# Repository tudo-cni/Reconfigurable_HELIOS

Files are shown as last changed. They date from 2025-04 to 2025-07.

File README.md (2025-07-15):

## Content of this Repository
This repository contains the code of the operation control center and SBC platform from our paper **Field Performance Evaluation of a
Mechatronic Reflector System in a Private mmWave Network Environment**.

If you use this code, please cite our original work in [Citation](#citation).

## Repository Structure
This paragraph describes the existing folder structure of the repository.
#### Main Folder
- **reconfigurable-helios-platform/**
  - Contains all project files and subfolders.  
##### Subfolders
- **Operation Control Center**
  - Contains all necessary files to run the operation control center
  - **angle mapping**
    - Contains the tables to convert the mechanical azimuth and elevation tilt angles alpha and beta to the corresponding servomotor angles from the top and bottom servomotor
  - **classes**
    - Contains the classes and methods for the operation control center
  - **configurations**
    - Configurations from the operation control center are saved in this folder in txt-files
  - **logos**
    - Contains the svg-files of TU Dortmund University and Communication Networks Institute logos for the operation control center
  - operation_control_center.py
    - Main file of the operation control center
- **Platform Code**
  - Contains the .py files, which run on the SBC

## Quick Start
#### Operation Control Center
This repository contains the code for the Operation Control Center, developed in Python.

To run the Operation Control Center, [NumPy](https://numpy.org/), [PySide6](https://pypi.org/project/PySide6/), to provide access to the QT6.0+ framework, and the [Qt-Material](https://qt-material.readthedocs.io/en/latest/index.html) packages are required.

The code has been tested with the following versions:
- Python: 3.13.0
- Numpy: 2.1.3
- PySide6: 6.9.0
- Qt-Material: 2.14

To start the operation control center, execute **"operation_control_center.py"**.

#### SBC Platform
To run the platform code, you must upload the necessary files from the "Platform Code" folder to the Raspberry Pi Pico, along with the two files "servo.py" and "pca9685.py" from the "[micropython-adafruit-pca9685](https://github.com/adafruit/micropython-adafruit-pca9685)" library.
Please note that these two files are not included in the folder and need to be downloaded from the specified library.

The "main.py" file will then be executed automatically upon starting the single-board computer (SBC).

## Acknowledgement
This work has been supported by the German Federal Ministry of Research, Technology and Space ([BMFTR](https://https://www.bundesregierung.de/breg-en/federal-government/ministries/federal-ministry-of-research-technology-and-space)) in the course of the
[6GEM Research Hub](https://www.6gem.de/en/) under the grant number 16KISK038.

## Citation
If you use this code in any of your publications, please cite our work (author's version) as:
```
@article{Haeger/etal/2025b,
	Author = {S. H{\"a}ger, M. Kaudewitz, F. Schmickmann, S. B{\"o}cker, and C. Wietfeld},
	Title = {Field Performance Evaluation of a Mechatronic Reflector System in a Private {mmWave} Network Environment},
	Journal = {IEEE Open Journal of the Communications Society},
	Month= jun, 
	Year = {2025},
	Vol = {6},
	Pages = {5005-5029},
	Doi = {10.1109/OJCOMS.2025.3572723},
	Project = {6GEM}, 
}
```

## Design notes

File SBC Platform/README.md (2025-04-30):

## SBC Platform
This folder contains the files that need to be uploaded to the SBC Platform, along with two additional files that are not included in this folder: "servo.py" and "pca9685.py" from the "[micropython-adafruit-pca9685](https://github.com/adafruit/micropython-adafruit-pca9685)" library.

Note: The values from the three calibrated positions of each servomotor obtained during the calibration process must be included in **calibration_function.py**!

- **main.py**
    - Is executed when the SBC platform is powered on.
- **wireless_module.py**
    - Initializes the wireless module of the SBC as an access point.
- **init_pca.py**
    - Initializes the two PCA9685 and the I2C connection between the PCAs and the SBC.
- **received_data_processing.py**
    - Method to convert received data string to numerical list.
- **calibration_function.py**
    - Method to calibrate the input values based on the calibration tables from the calibration procedure.
    - Note: The values from the calibration process are included here!
- **set_angle_functions.py**
    - Methods to set the PWM value of the corresponding PCA9685 outputs in order to achieve the desired mechanical tilt of the reflecting surface.

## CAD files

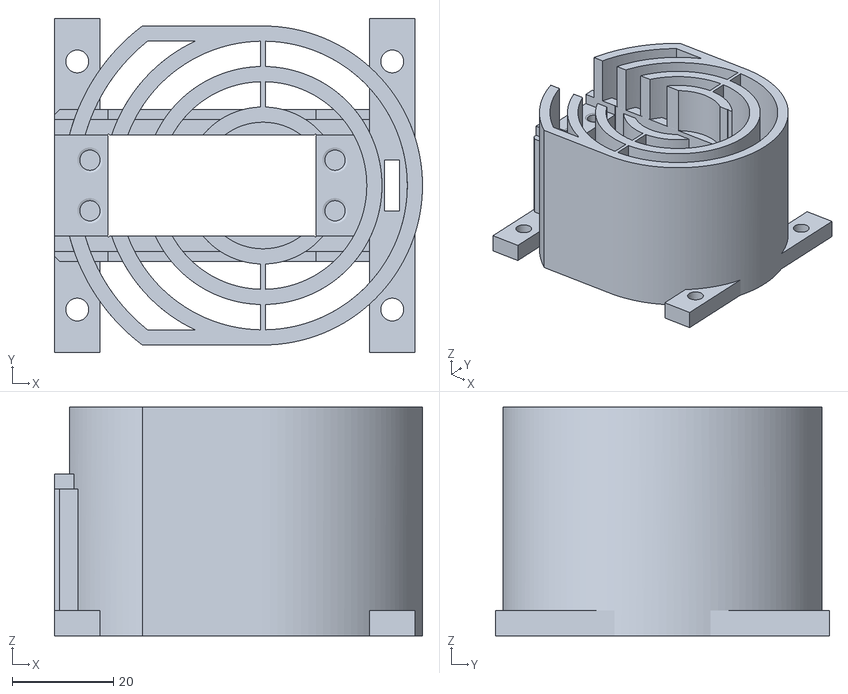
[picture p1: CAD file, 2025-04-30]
STL Module Files/Module_Base.stl
72.7 x 66.0 x 45.2

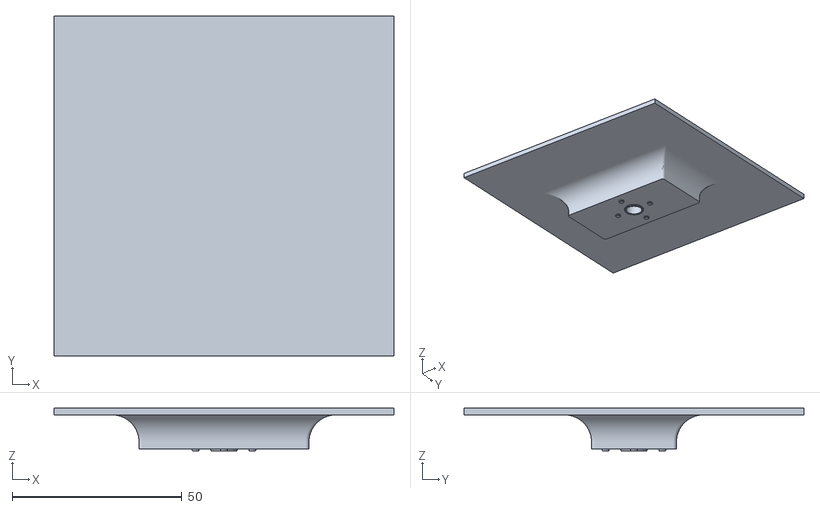
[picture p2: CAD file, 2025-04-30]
STL Module Files/Reflecting_Surface_Square10x10.stl
100.0 x 100.0 x 12.6

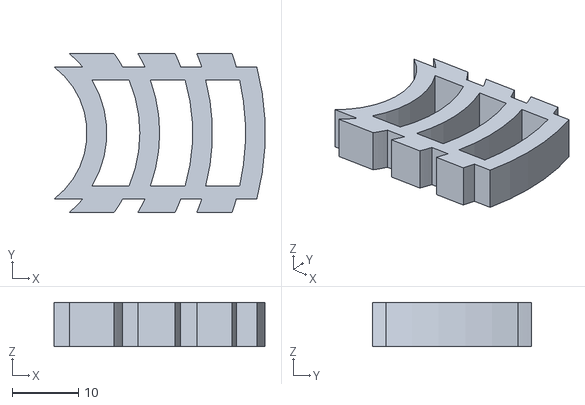
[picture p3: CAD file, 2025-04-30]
STL Module Files/Module_Plug.stl
31.9 x 24.0 x 6.70

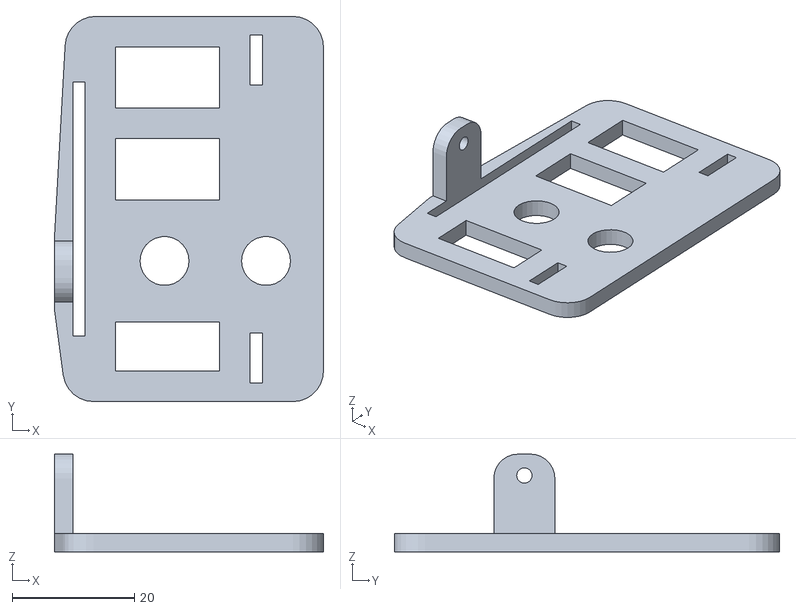
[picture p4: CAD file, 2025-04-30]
STL Module Files/Module_Plate.stl
44.0 x 63.0 x 16.0

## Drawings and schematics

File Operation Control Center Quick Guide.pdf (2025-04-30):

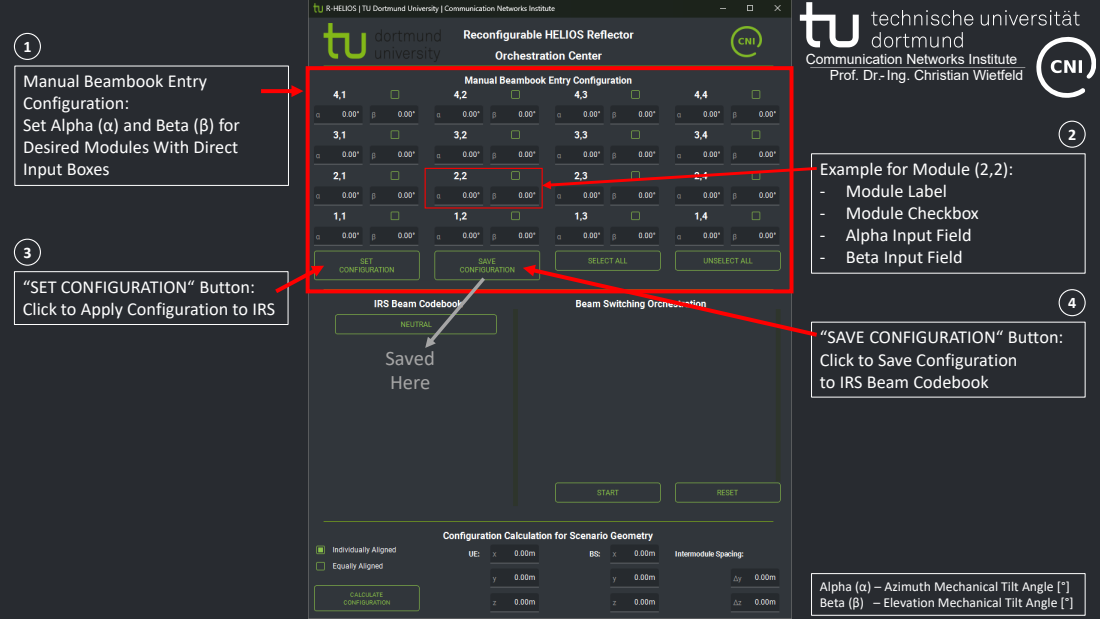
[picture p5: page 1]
Input Boxes; Example for Module (2,2):; Saved Here

Manual Beambook Entry
Configuration:
Set Alpha (α) and Beta (β) for
Desired Modules With Direct

- Module Label
- Module Checkbox
- Alpha Input Field
- Beta Input Field

“SET CONFIGURATION“ Button:
Click to Apply Configuration to IRS

“SAVE CONFIGURATION“ Button:
Click to Save Configuration
to IRS Beam Codebook

Alpha (α) – Azimuth Mechanical Tilt Angle [°]
Beta (β) – Elevation Mechanical Tilt Angle [°]

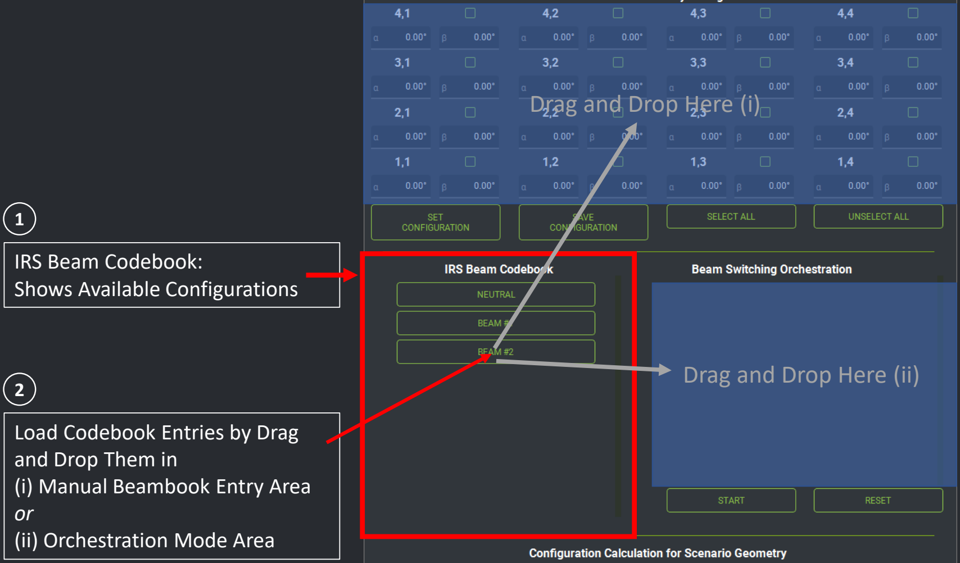
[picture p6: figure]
IRS Beam Codebook: Shows Available Configurations; Load Codebook Entries by Drag and Drop Them in (i) Manual Beambook Entry Area or (ii) Orchestration Mode Area; Drag and Drop Here (i); Drag and Drop Here (ii)

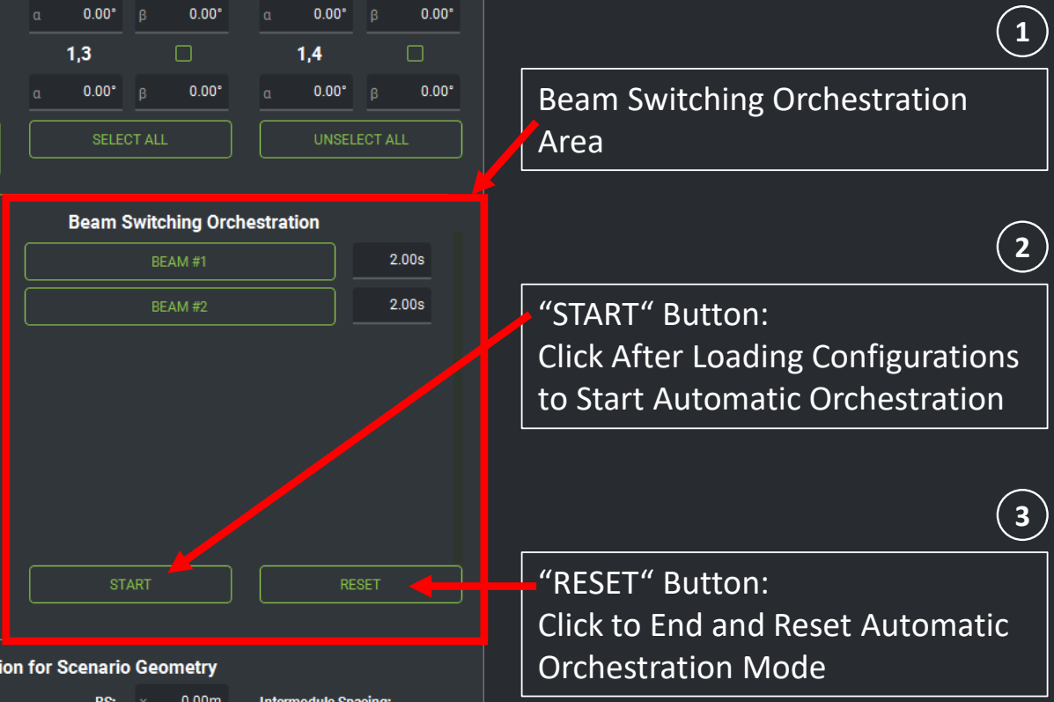
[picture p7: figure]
Beam Switching Orchestration Area; “START“ Button: Click After Loading Configurations to Start Automatic Orchestration; “RESET“ Button: Click to End and Reset Automatic Orchestration Mode
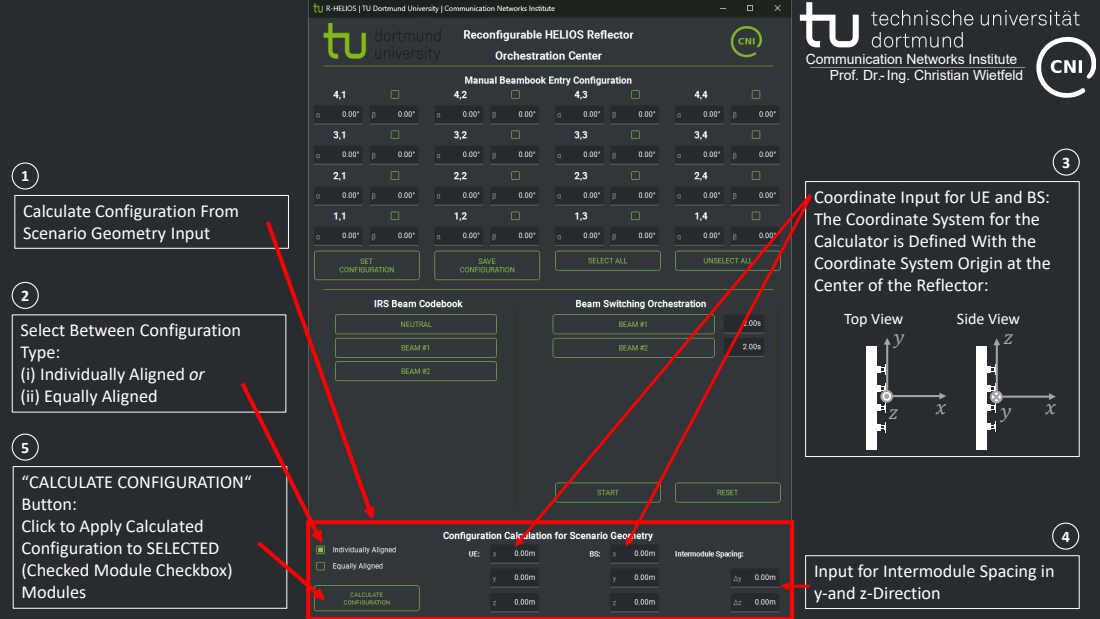
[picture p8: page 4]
Input for Intermodule Spacing in y-and z-Direction yz; Top View; Side View

Modules ¹²
Calculate Configuration From
Scenario Geometry Input

Coordinate Input for UE and BS:
The Coordinate System for the
Calculator is Defined With the
Coordinate System Origin at the
Center of the Reflector

Select Between Configuration
Type:
(i) Individually Aligned or
(ii) Equally Aligned

“CALCULATE CONFIGURATION“
Button:
Click to Apply Calculated
Configuration to SELECTED (Checked Module Checkbox)

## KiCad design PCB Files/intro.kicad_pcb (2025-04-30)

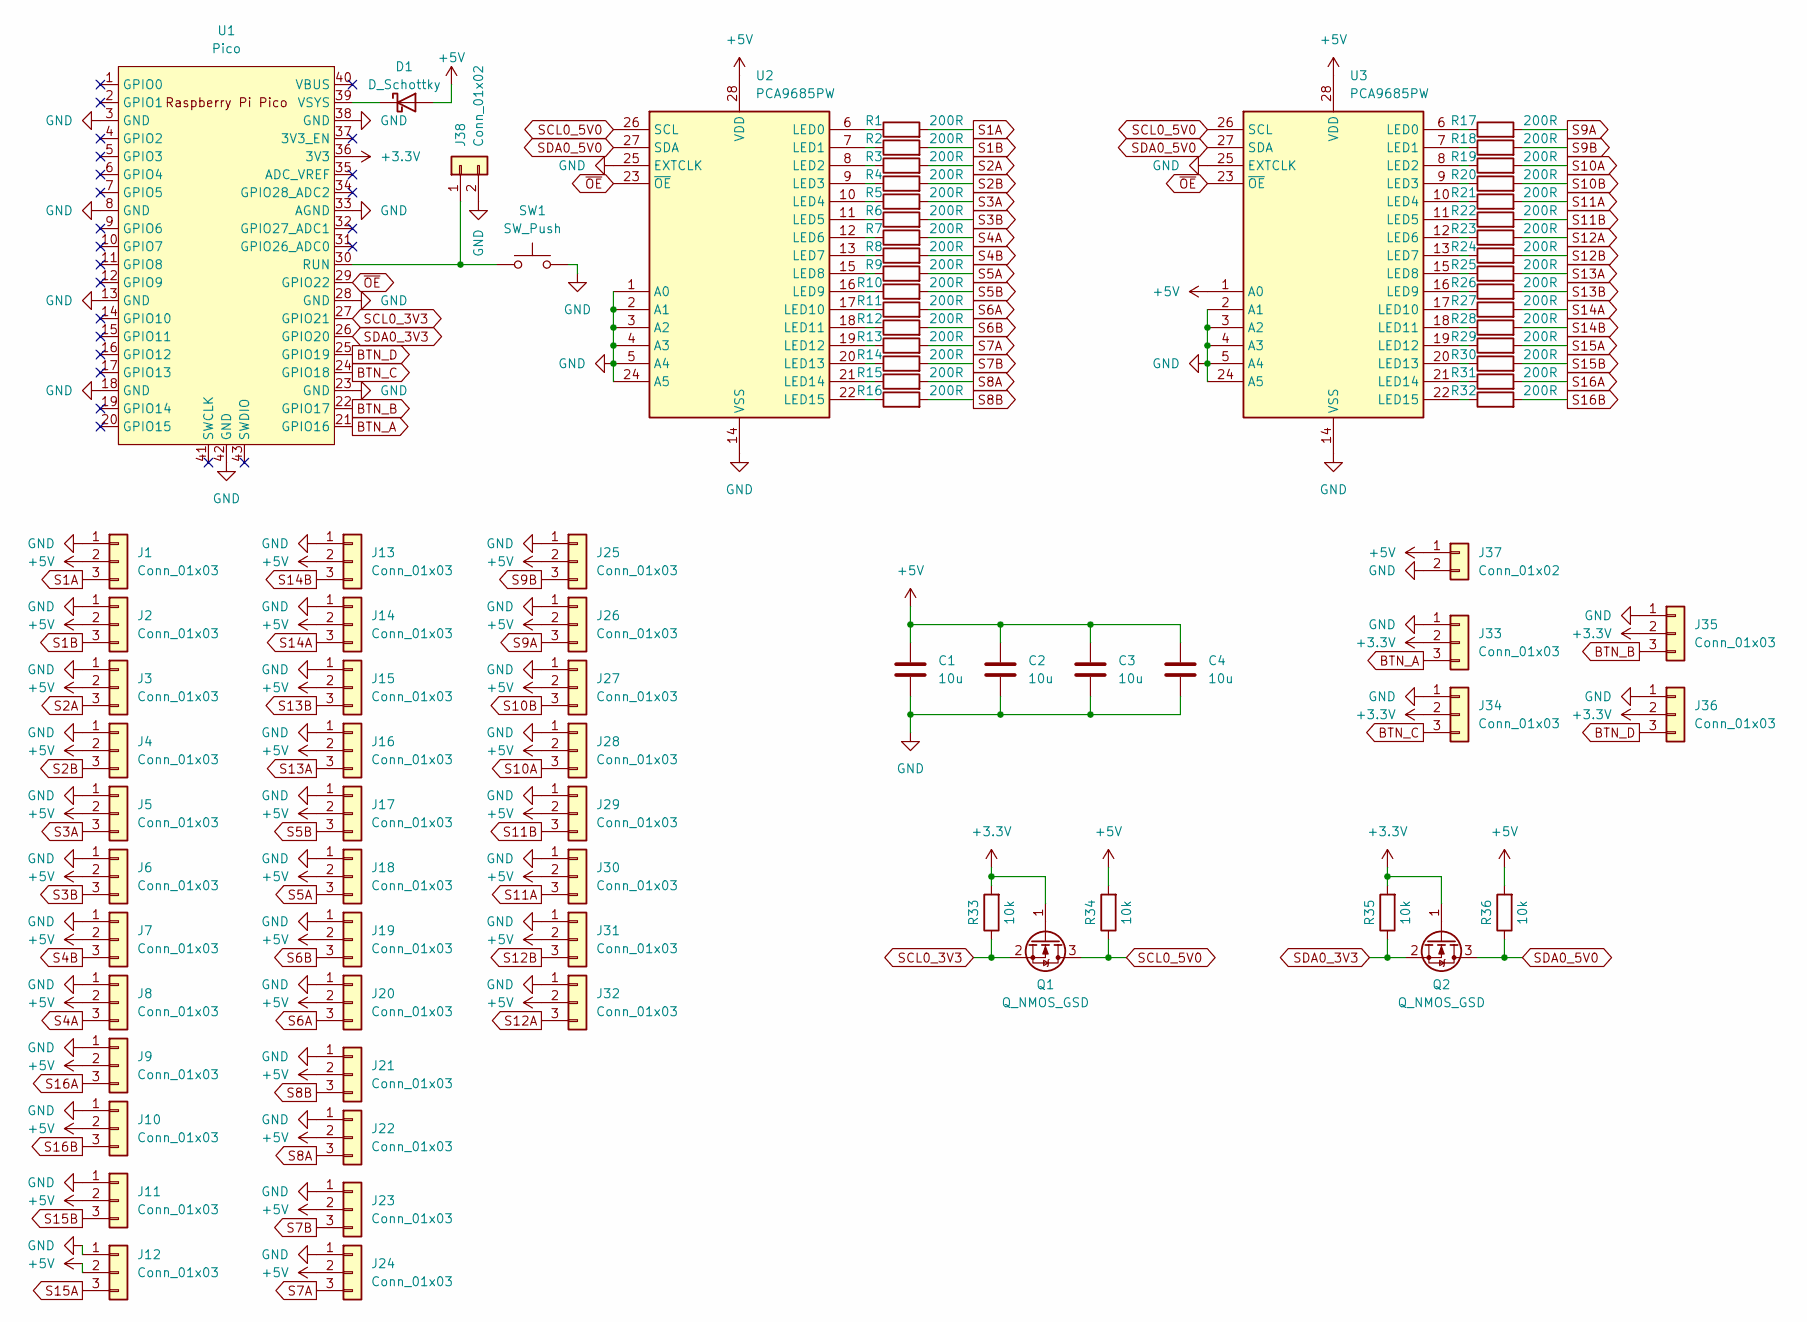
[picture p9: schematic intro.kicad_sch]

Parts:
C1, C2, C3, C4: 10u; C_0603_1608Metric
D1: D_Schottky; D_SOD-323_HandSoldering
J1, J2, J3, J4, J5, J6, J7, J8, J9, J10, J11, J12, J13, J14, J15, J16, J17, J18, J19, J20, J21, J22, J23, J24, J25, J26, J27, J28, J29, J30, J31, J32, J33, J34, J35, J36: Conn_01x03; PinHeader_1x03_P2.54mm_Vertical
J37: Conn_01x02; AMASS_XT60PW-M_1x02_P7.20mm_Horizontal
J38: Conn_01x02; PinHeader_1x02_P2.54mm_Vertical
Q1, Q2: Q_NMOS_GSD; SOT-23-3
R1, R2, R3, R4, R5, R6, R7, R8, R9, R10, R11, R12, R13, R14, R15, R16, R17, R18, R19, R20, R21, R22, R23, R24, R25, R26, R27, R28, R29, R30, R31, R32: 200R; R_0603_1608Metric
R33, R34, R35, R36: 10k; R_0603_1608Metric
SW1: SW_Push; SW_SPST_TL3342
U1: Pico; RPi_Pico_W_SMD_TH
U2, U3: PCA9685PW; TSSOP-28_4.4x9.7mm_P0.65mm

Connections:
+3.3V: J33.2, J34.2, J35.2, J36.2, Q1.1 (G), Q2.1 (G), R33.2, R35.2, U1.36 (3V3)
+5V: C1.1, C2.1, C3.1, C4.1, D1.2 (A), J1.2, J2.2, J3.2, J4.2, J5.2, J6.2, J7.2, J8.2, J9.2, J10.2, J11.2, J12.2, J13.2, J14.2, J15.2, J16.2, J17.2, J18.2, J19.2, J20.2, J21.2, J22.2, J23.2, J24.2, J25.2, J26.2, J27.2, J28.2, J29.2, J30.2, J31.2, J32.2, J37.1, R34.2, R36.2, U2.28 (VDD), U3.1 (A0), U3.28 (VDD)
BTN_A: J33.3, U1.21 (GPIO16)
BTN_B: J35.3, U1.22 (GPIO17)
BTN_C: J34.3, U1.24 (GPIO18)
BTN_D: J36.3, U1.25 (GPIO19)
GND: C1.2, C2.2, C3.2, C4.2, J1.1, J2.1, J3.1, J4.1, J5.1, J6.1, J7.1, J8.1, J9.1, J10.1, J11.1, J12.1, J13.1, J14.1, J15.1, J16.1, J17.1, J18.1, J19.1, J20.1, J21.1, J22.1, J23.1, J24.1, J25.1, J26.1, J27.1, J28.1, J29.1, J30.1, J31.1, J32.1, J33.1, J34.1, J35.1, J36.1, J37.2, J38.2, SW1.2, U1.3 (GND), U1.8 (GND), U1.13 (GND), U1.18 (GND), U1.23 (GND), U1.28 (GND), U1.33 (AGND), U1.38 (GND), U1.42 (GND), U2.1 (A0), U2.2 (A1), U2.3 (A2), U2.4 (A3), U2.5 (A4), U2.14 (VSS), U2.24 (A5), U2.25 (EXTCLK), U3.2 (A1), U3.3 (A2), U3.4 (A3), U3.5 (A4), U3.14 (VSS), U3.24 (A5), U3.25 (EXTCLK)
unnamed: D1.1 (K), U1.39 (VSYS)
unnamed: J38.1, SW1.1, U1.30 (RUN)
unnamed: R1.1, U2.6 (LED0)
unnamed: R2.1, U2.7 (LED1)
unnamed: R3.1, U2.8 (LED2)
unnamed: R4.1, U2.9 (LED3)
unnamed: R5.1, U2.10 (LED4)
unnamed: R6.1, U2.11 (LED5)
unnamed: R7.1, U2.12 (LED6)
unnamed: R8.1, U2.13 (LED7)
unnamed: R9.1, U2.15 (LED8)
unnamed: R10.1, U2.16 (LED9)
unnamed: R11.1, U2.17 (LED10)
unnamed: R12.1, U2.18 (LED11)
unnamed: R13.1, U2.19 (LED12)
unnamed: R14.1, U2.20 (LED13)
unnamed: R15.1, U2.21 (LED14)
unnamed: R16.1, U2.22 (LED15)
unnamed: R17.1, U3.6 (LED0)
unnamed: R18.1, U3.7 (LED1)
unnamed: R19.1, U3.8 (LED2)
unnamed: R20.1, U3.9 (LED3)
unnamed: R21.1, U3.10 (LED4)
unnamed: R22.1, U3.11 (LED5)
unnamed: R23.1, U3.12 (LED6)
unnamed: R24.1, U3.13 (LED7)
unnamed: R25.1, U3.15 (LED8)
unnamed: R26.1, U3.16 (LED9)
unnamed: R27.1, U3.17 (LED10)
unnamed: R28.1, U3.18 (LED11)
unnamed: R29.1, U3.19 (LED12)
unnamed: R30.1, U3.20 (LED13)
unnamed: R31.1, U3.21 (LED14)
unnamed: R32.1, U3.22 (LED15)
S1A: J1.3, R1.2
S1B: J2.3, R2.2
S2A: J3.3, R3.2
S2B: J4.3, R4.2
S3A: J5.3, R5.2
S3B: J6.3, R6.2
S4A: J8.3, R7.2
S4B: J7.3, R8.2
S5A: J18.3, R9.2
S5B: J17.3, R10.2
S6A: J20.3, R11.2
S6B: J19.3, R12.2
S7A: J24.3, R13.2
S7B: J23.3, R14.2
S8A: J22.3, R15.2
S8B: J21.3, R16.2
S9A: J26.3, R17.2
S9B: J25.3, R18.2
S10A: J28.3, R19.2
S10B: J27.3, R20.2
S11A: J30.3, R21.2
S11B: J29.3, R22.2
S12A: J32.3, R23.2
S12B: J31.3, R24.2
S13A: J16.3, R25.2
S13B: J15.3, R26.2
S14A: J14.3, R27.2
S14B: J13.3, R28.2
S15A: J12.3, R29.2
S15B: J11.3, R30.2
S16A: J9.3, R31.2
S16B: J10.3, R32.2
SCL0_3V3: Q1.2 (S), R33.1, U1.27 (GPIO21)
SCL0_5V0: Q1.3 (D), R34.1, U2.26 (SCL), U3.26 (SCL)
SDA0_3V3: Q2.2 (S), R35.1, U1.26 (GPIO20)
SDA0_5V0: Q2.3 (D), R36.1, U2.27 (SDA), U3.27 (SDA)
~OE: U1.29 (GPIO22), U2.23 (~OE), U3.23 (~OE)

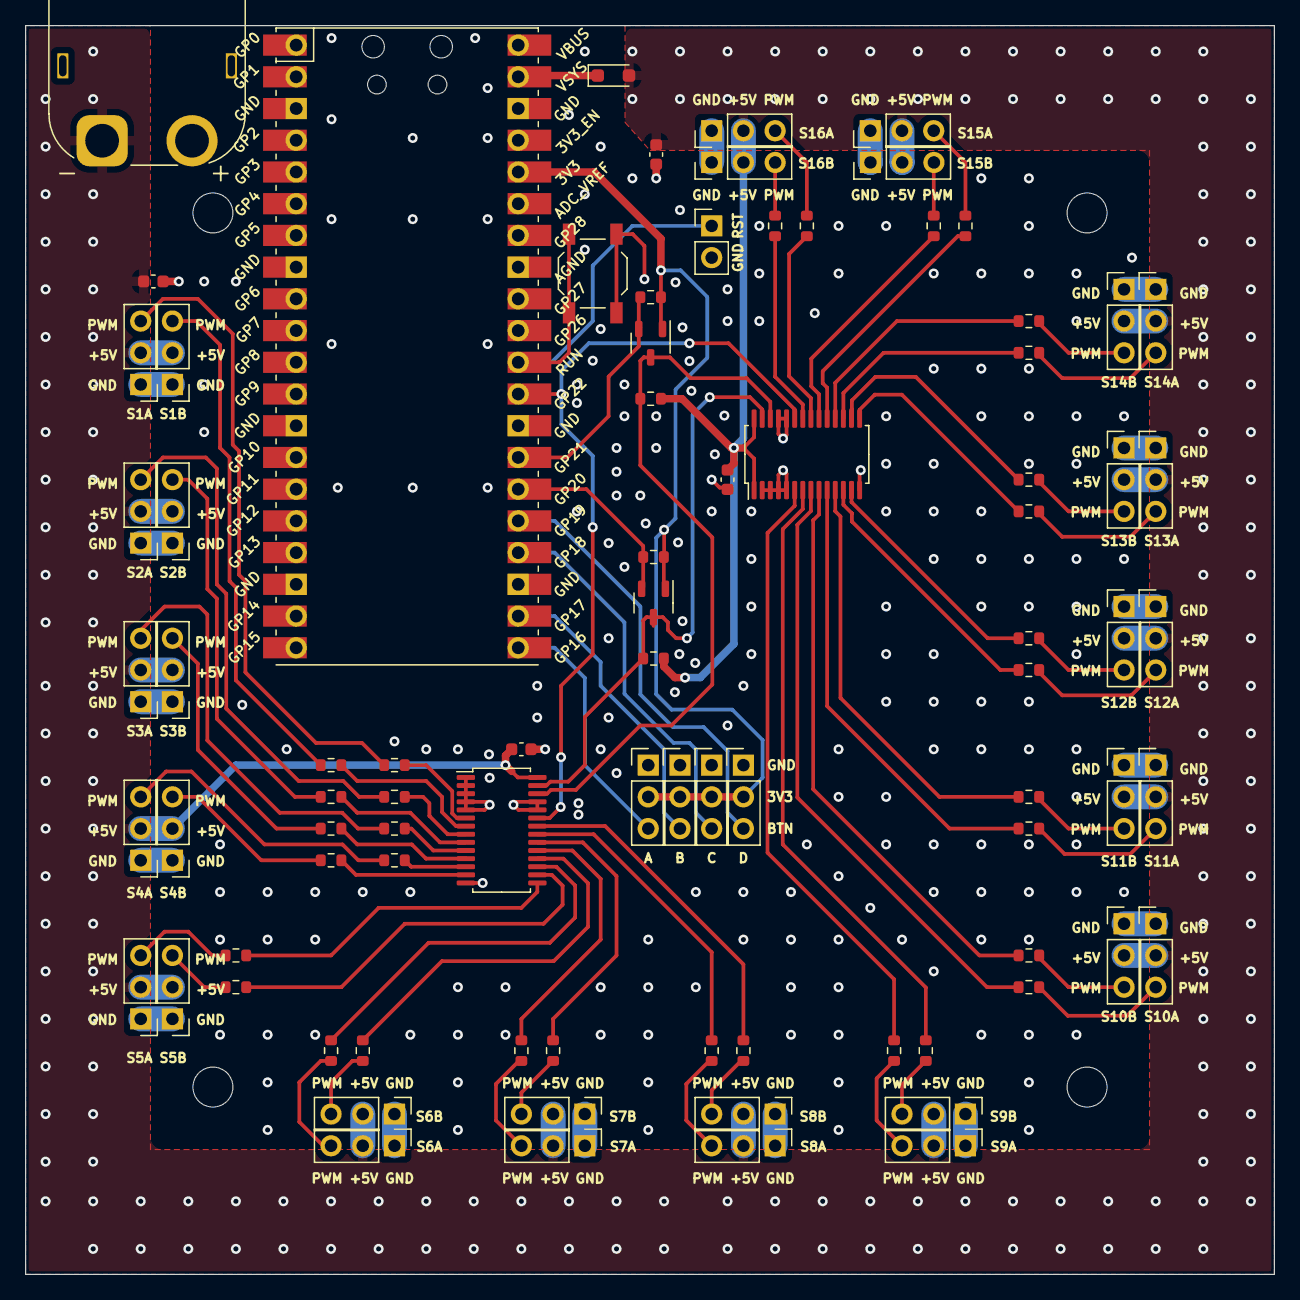
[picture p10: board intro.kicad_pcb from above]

Board: 4 copper layers, 100.0 x 100.0 mm, 85 parts (0 on the bottom side), 78 nets.

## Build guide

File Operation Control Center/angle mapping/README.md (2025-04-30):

## Angle Mapping Folder
This folder contains the angle mapping tables to convert azmuth tilt angle alpha and eleation tilt angle beta from the reflecting urface in the corresponding servomotor angles for the top and bottom servomotor.

Each file contains the table for the alpha angle of the file name and all beta angles from -60.00° up to 60.00° as a numpy file. 
For example the file "angle_map_alpha_5980.npy" contains for alpha=59.80° and all beta angles, with the first line of the file conatining the angles fop beta=-60.00° and the last line for beta=60.00° in 0.01° steps.

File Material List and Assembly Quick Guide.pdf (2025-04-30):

The Authors | Slide 1

Communication Networks Institute Prof. Dr.-Ing. Christian Wietfeld

Field Performance Evaluation of a Mechatronic Reflector System in a Private mmWave Network Environment

# Material List

| Quantity | Part | Assembly Step
1 | 11 | Aluminum Profile 20x20 Groove 6 B-Type, 1m | 1
2 | 16 | Internal 90° Angle/Bracket Groove 6 B-Type M5
3 | 32 | Screw M5x5
4 | 16 | Pan & Tilt Kit, cf. Paper
5 | 16 | Long “C“ Bracket (51mm(L) X 24mm(W) X 57mm(H))
6 | 16 | 3D-Printed Module (Base, Plug and Plate)
7 | 64 | M3x5.7 3D-Printing Threaded Insert
8 | 64 | Screw M3x7
9 | 16 | 3D-Printed Reflecting Surface
10 | 16 | Screw M5x8, with washer
11 | 16 | M5x9.5 3D-Printing Threaded Insert
12 | 1 | SBC (Raspberry Pi Pico W) | 3
13 | 2 | 16-Channel Pulse-Width Modulation Controller (PCA9685)
14 | 1 | Designed PCB
15 | 64 | Screw M3x7 | 4
16 | 64 | M3 Slot Nuts Groove 6
17 | 32 | Servomotor Extension Cable JR Male to Female, 1m | 5
18 | 1 | 5V Power Supply

2

# 1. Assembly Instruction – Frame

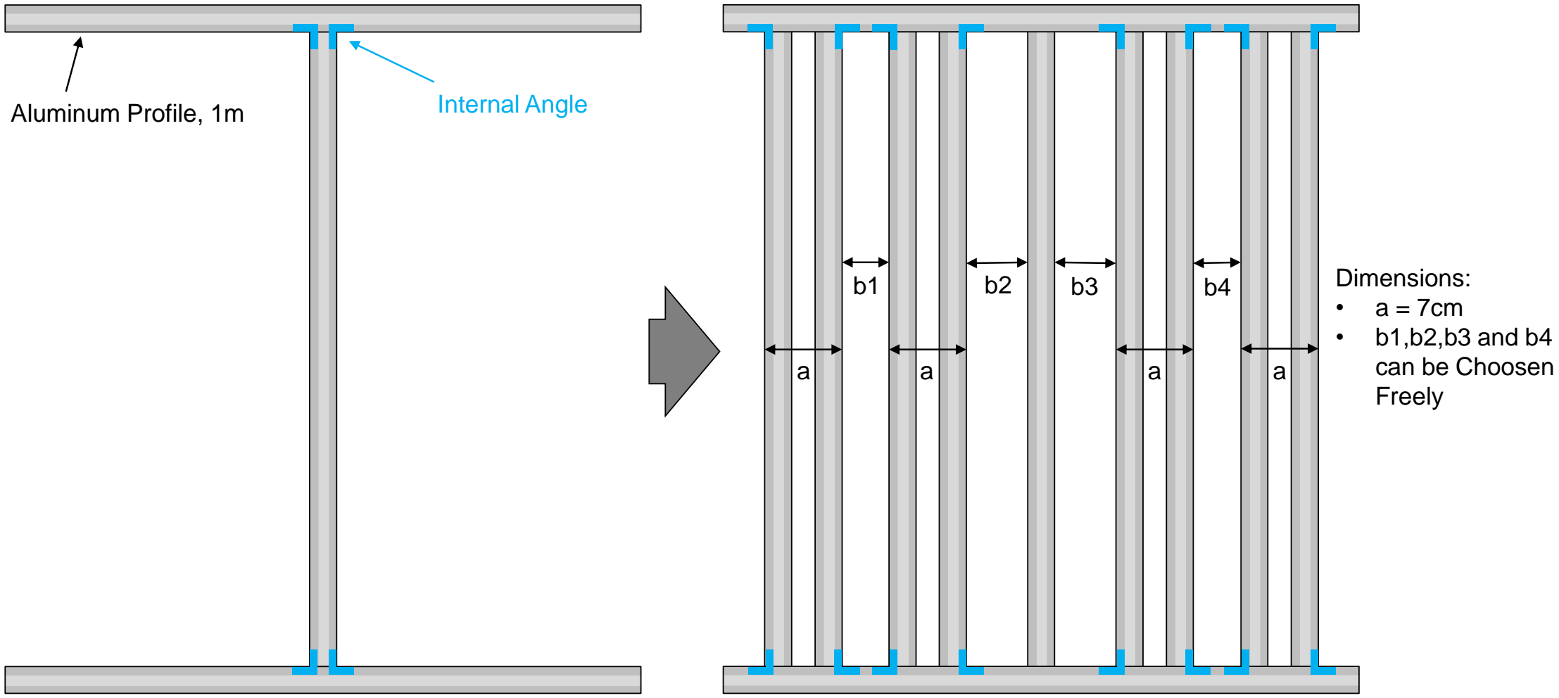
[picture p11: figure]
Aluminum Profile, 1m; Internal Angle; Dimensions:; • a = 7cm • b1,b2,b3 and b4 can be Choosen Freely

# 2. Assembly Instruction – Module (1)

1. Assemble 16 Modules, Each Consisting of Three 3D-Printed Components (Base, Plug, Plate) Along With the Pan & Tilt Kit)

## 2. Assemble in the Following Order:

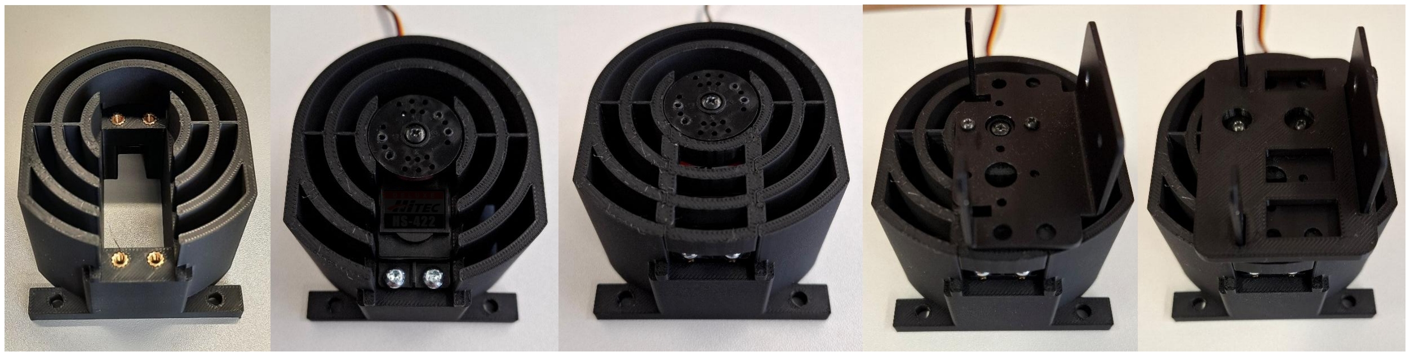
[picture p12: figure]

### 1. Start With the 3D-Printed Module Base with 4 M3x5.7 Threaded Inserts

### 2. Place First Servomotor in Module Base and Fixate it With 4 M3x7 Screws

### 3. Press the 3D-Printed Module Plug Into the Gap Until it Fits Cleanly With the Edges

### 4. Fixate the Multi-Purpose Servo Bracket From the Pan & Tilt Kit on the Servomotor

### 4. Place the 3D-Printed Module Plate on the Bracket

# 2. Assembly Instruction – Module (2)

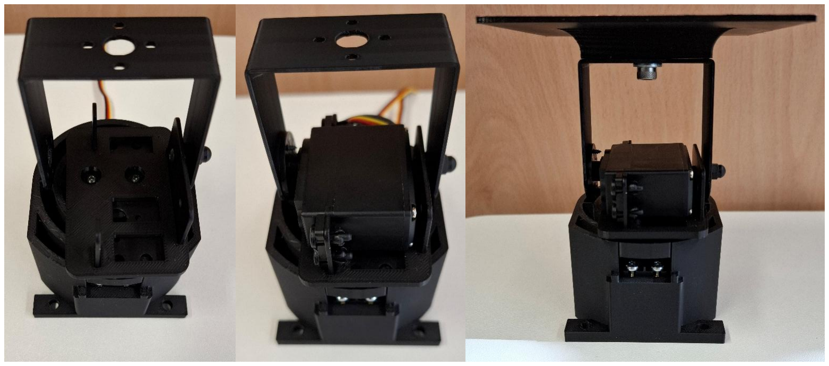
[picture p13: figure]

### 5. Mount Long “C“ Bracket Instead of Short “C“ Bracket From the Pan & Tilt Kit

### 6. Mount Second Servomotor as Specified by the Pan & Tilt Kit

### 7. Prepare the 3D-Printed Reflecting Surface With a M5x9.5 Threaded Insert. Mount the Reflecting Surface on the “C“ Bracket with

One M5x8 Screw With Washer.

3. On the 3D-Printed Reflecting Surface Self-Adhesive Copper Tape can be Applied or, for Example, a Conductive Coating can be

## Spray-Painted, to Achieve Desired Reflection Characteristics

# 3. Assembly Instruction – SBC and PCB Circuit Diagram

## 1. To Control the 32 Servomotor a SBC

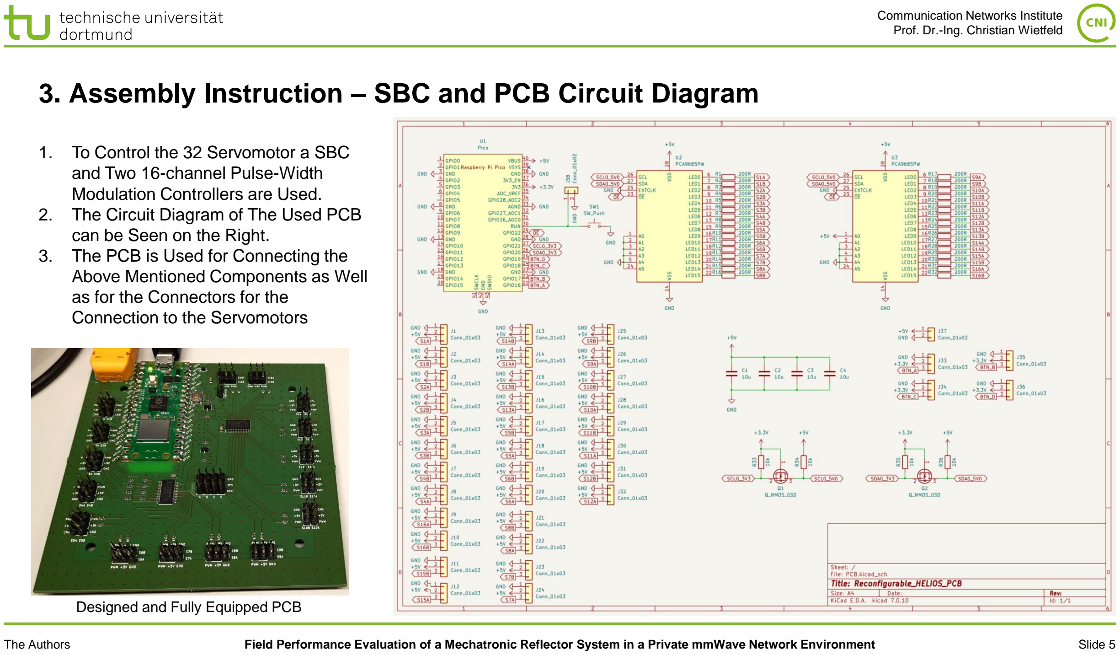
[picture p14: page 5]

## and Two 16-channel Pulse-Width

Modulation Controllers are Used.

## 2. The Circuit Diagram of The Used PCB

can be Seen on the Right.

## 3. The PCB is Used for Connecting the Above Mentioned Components as Well as for the Connectors for the Connection to the Servomotors

### Designed and Fully Equipped PCB

# 4. Assembly Instruction – Mount Modules on Frame

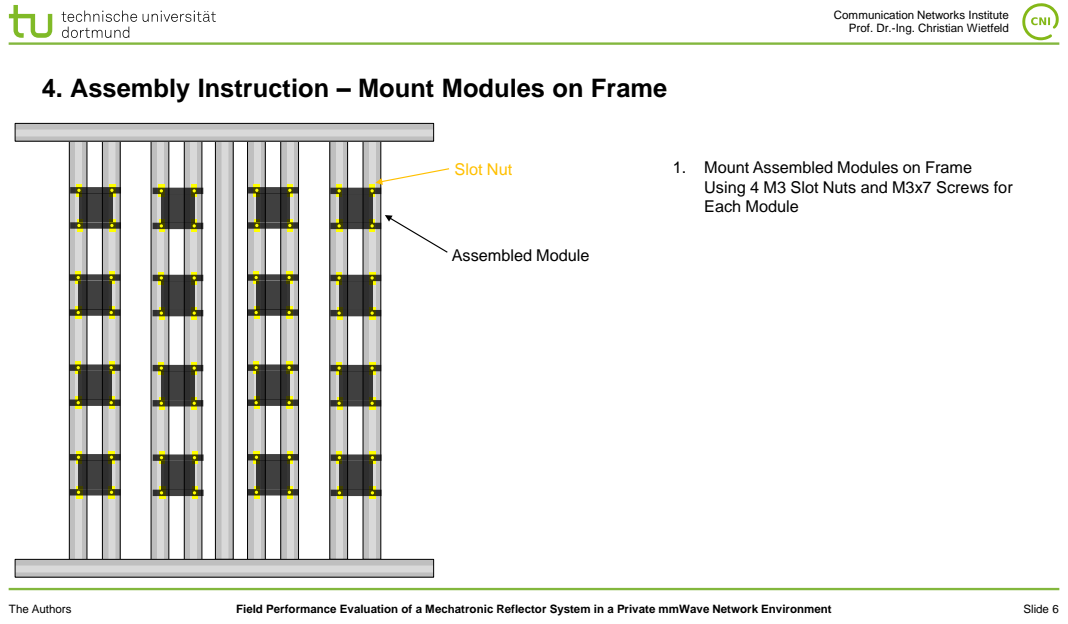
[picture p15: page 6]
Slot Nut; Assembled Module

1. Mount Assembled Modules on Frame
Using 4 M3 Slot Nuts and M3x7 Screws for
Each Module

# 5. Assembly Instruction – Connection Overview

## PCB Slot Overview

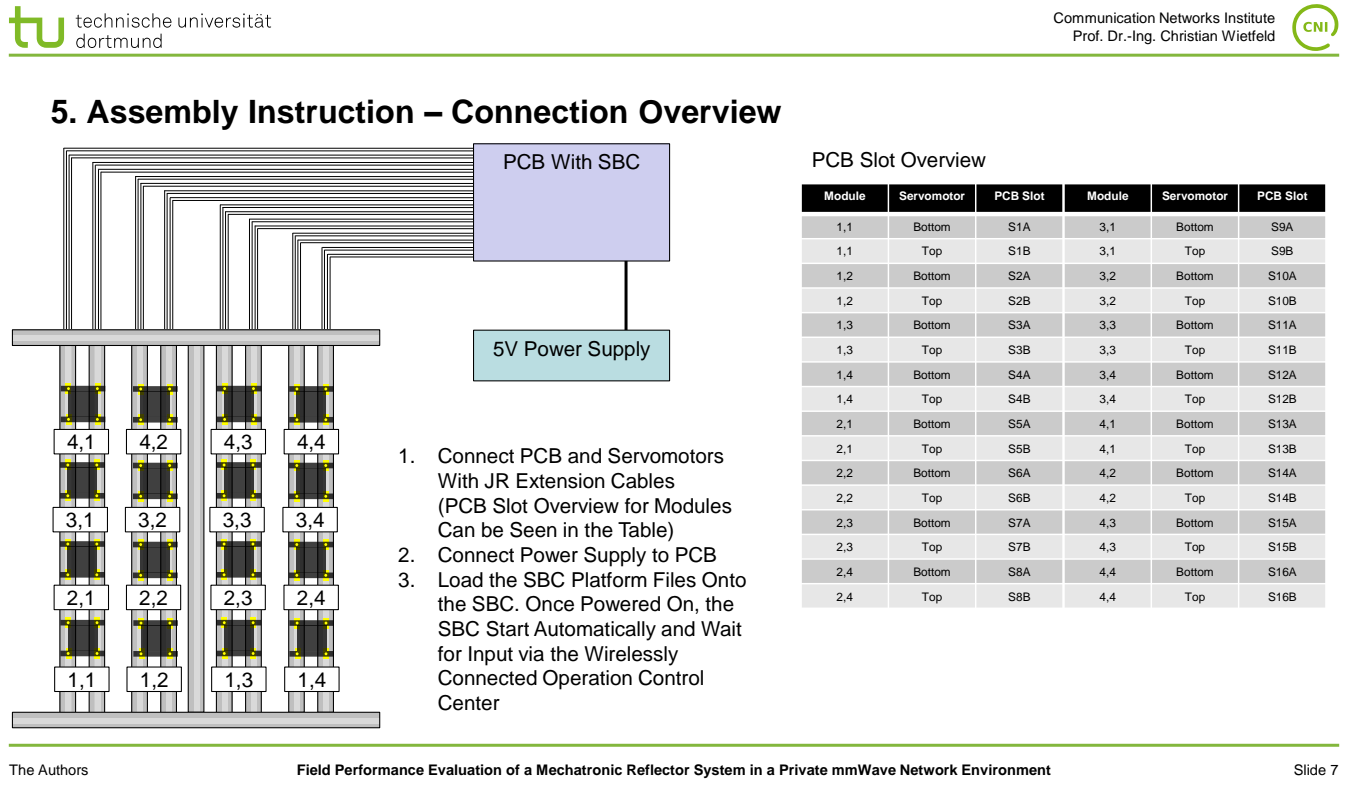
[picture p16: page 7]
5V Power Supply

PCB With SBC

Module | Servomotor | PCB Slot | Module | Servomotor | PCB Slot

1,1 | Bottom | S1A | 3,1 | Bottom | S9A

1,1 | Top | S1B | 3,1 | Top | S9B

1,2 | Bottom | S2A | 3,2 | Bottom | S10A

1,2 | Top | S2B | 3,2 | Top | S10B

1,3 | Bottom | S3A | 3,3 | Bottom | S11A

1,3 | Top | S3B | 3,3 | Top | S11B

1,4 | Bottom | S4A | 3,4 | Bottom | S12A

1,4 | Top | S4B | 3,4 | Top | S12B

2,1 | Bottom | S5A | 4,1 | Bottom | S13A

1. Connect PCB and Servomotors
With JR Extension Cables
(PCB Slot Overview for Modules
Can be Seen in the Table)
2. Connect Power Supply to PCB
3. Load the SBC Platform Files Onto
the SBC. Once Powered On, the
SBC Start Automatically and Wait
for Input via the Wirelessly
Connected Operation Control
Center

2,1 | Top | S5B | 4,1 | Top | S13B

2,2 | Bottom | S6A | 4,2 | Bottom | S14A

2,2 | Top | S6B | 4,2 | Top | S14B

2,3 | Bottom | S7A | 4,3 | Bottom | S15A

2,3 | Top | S7B | 4,3 | Top | S15B

2,4 | Bottom | S8A | 4,4 | Bottom | S16A

2,4 | Top | S8B | 4,4 | Top | S16B

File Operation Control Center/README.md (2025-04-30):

## Operation Control Center
This folder contains all necessary files to run the operation control center.

To start the Operation Control Center, execute **"operation_control_center.py"**.

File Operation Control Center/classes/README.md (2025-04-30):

## Classes Folder
This folder contains the classes to run the widgets in the main window of the application.

beambook: Files, which include the different widgets for the IRS Beam Codebook
orchestration: Files, which include the functionality and widgets for the orchestration mode
connection_handling: Files, which handle the wireless connection between the operation control dashboard and SBC
svg_file_handling: Files, which are needed to include svg-files in the application.

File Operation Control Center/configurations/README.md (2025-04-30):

## Configurations Folder
In this folder the configurations are saved in .txt files.

Each file contains the 16 alpha and beta angles of the configurations in a string seperated by ';'.

The string is constructed in this way:
"alpha_module_1_1;beta_module_1_1;alpha_module_1_2;beta_module_1_2;...;alpha_module_4_3;beta_module_4_3;alpha_module_4_4;beta_module_4_4"

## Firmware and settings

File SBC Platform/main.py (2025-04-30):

# Author: Marcel Kaudewitz
# Affiliation: TU Dortmund University, Communication Networks Institute (CNI)
# Contact: marcel.kaudewitz@tu-dortmund.de
# Date: March 3, 2025

import machine
import time

import wireless_module
import init_pca
import set_angle_functions
import received_data_processing


# Init Wireless Module and Server Socket
wireless_module.init_wireless_module()
server = wireless_module.start_server()
  
# Init PCAs
pca_a, pca_b = init_pca.init_pca()

# Init Pi LED
led = machine.Pin("LED", machine.Pin.OUT)
temp_packet_number = 0
set_angle_functions.set_pca_outputs([1,0,0,0,0,0,0,0,0,0,0,0,0,0,0,0,0,0,0,0,0,0,0,0,0,0,0,0,0,0,0,0,0,0,0], pca_a, pca_b)

time.sleep(1.0)
set_angle_functions.pca_release_all(pca_a, pca_b)

# Set LED ON, Pi Ready
led.on()

# Listen On Connection, Wait For Input By Operation Control
while True:
    try:
        conn, byte_data = wireless_module.server_listen(server)
        received_degrees = received_data_processing.data_processing(byte_data)     
        if received_degrees[1] >= temp_packet_number or received_degrees[1] == 0:
            set_angle_functions.set_pca_outputs(received_degrees, pca_a, pca_b)
            temp_packet_number = received_degrees[1]
        conn.send(b'OK')
        conn.close()
        print('Connection closed')
        print()
        print('Finished')
        
    except OSError as e:
        break
    except (KeyboardInterrupt):
        break

try: conn.close()
except NameError: pass
server.close()


                    
    

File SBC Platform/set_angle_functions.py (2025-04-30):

# Author: Marcel Kaudewitz
# Affiliation: TU Dortmund University, Communication Networks Institute (CNI)
# Contact: marcel.kaudewitz@tu-dortmund.de
# Date: March 3, 2025

import calibration_function

# Get PCA Index for Servomotor Input
def get_pca_index(servo):
    if servo[0] == 1 or servo[0] == 2: 
        pca_index = 0
    elif servo[0] == 3 or servo[0] == 4: 
        pca_index = 1
  
    return pca_index

# Map Module 2D-Naming Matrix to 1D-Naming From 0-15
def get_servo_index(servo):
    if servo == [1,1]:
        servo_index = 0
    elif servo == [1,2]:
        servo_index = 2
    elif servo == [1,3]:
        servo_index = 4
    elif servo == [1,4]:
        servo_index = 6
    elif servo == [2,1]:
        servo_index = 8
    elif servo == [2,2]:
        servo_index = 10
    elif servo == [2,3]:
        servo_index = 12
    elif servo == [2,4]:
        servo_index = 14
    elif servo == [3,1]:
        servo_index = 0
    elif servo == [3,2]:
        servo_index = 2       
    elif servo == [3,3]:
        servo_index = 4
    elif servo == [3,4]:
        servo_index = 6          
    elif servo == [4,1]:
        servo_index = 8
    elif servo == [4,2]:
        servo_index = 10        
    elif servo == [4,3]:
        servo_index = 12
    elif servo == [4,4]:
        servo_index = 14

    return servo_index

# Set PCA Outputs for each Servomotor
def set_pca_outputs(received_degrees, pca_a, pca_b):
    # Normalize Data from range (-90,90) to (0,180)
    for k in range(3,len(received_degrees)):
        received_degrees[k] = received_degrees[k] + 90
    # Check If Values Should Be Calibrated
    if received_degrees[0] == 1:
        k = 3
        for n in range(1,5):
            for m in range(1,5):
                received_degrees[k] = calibration_function.degree_calibration((n,m),'bottom_servomotor',received_degrees[k])
                received_degrees[k+1] = calibration_function.degree_calibration((n,m),'top_servomotor',received_degrees[k+1])
                k = k + 2
    # Set Degree Values At PCA
    k = 3
    for n in range(1,5):
        for m in range(1,5):
            pca_index = get_pca_index([n,m])
            servo_index = get_servo_index([n,m])
            # Distinguish Between the Two PCAs
            if pca_index == 0:
                pca_a.position(servo_index, degrees=received_degrees[k])
                pca_a.position(servo_index + 1, degrees=received_degrees[k + 1])
            elif pca_index == 1:
                pca_b.position(servo_index, degrees=received_degrees[k])
                pca_b.position(servo_index + 1, degrees=received_degrees[k + 1])
                
# Release All PCA Outputs to None
def pca_release_all(pca_a, pca_b):
    for n in range(1,5):
        for m in range(1,5):
            pca_index = get_pca_index([n,m])
            servo_index = get_servo_index([n,m])
            # Distinguish Between the Two PCAs
            if pca_index == 0:
                pca_a.release(servo_index)
                pca_a.release(servo_index + 1)     
            elif pca_index == 1:
                pca_b.release(servo_index)
                pca_b.release(servo_index + 1)  
